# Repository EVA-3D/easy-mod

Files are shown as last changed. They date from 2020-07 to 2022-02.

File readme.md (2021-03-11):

# Rat Rig V-core Pro "Easy Mod"

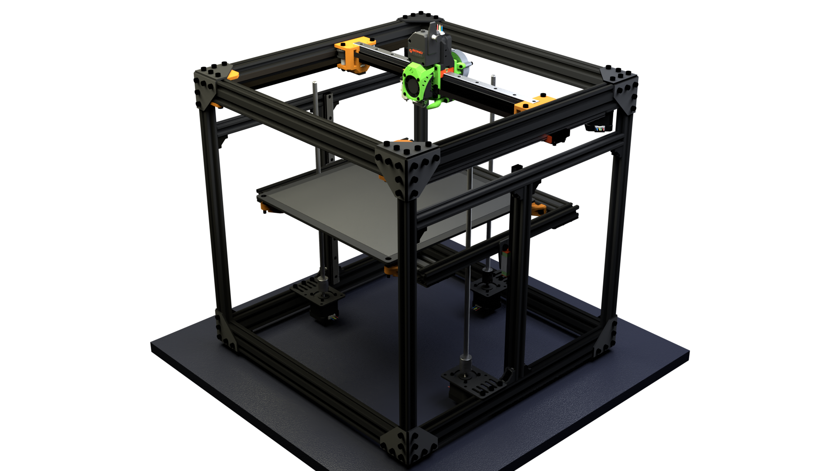
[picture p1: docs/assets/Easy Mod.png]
base


## What this is

Nothing on it's own really - nice selling point I know - but this is a part of a bigger project - the base to use the **[EVA](https://github.com/pkucmus/EVA/) carriage platform** is one example.

The files are in the stl directory, you can download them all as a zip file [here](https://github.com/pkucmus/EVA/archive/master.zip).

## Where to get one

I'm happy to anounce that Rat Rig decided to sell their V-core with Easy Mod out of the box. Check them out to get your V-core Pro with Easy Mod.

## Source

You can find the source in [this Onshape document](https://cad.onshape.com/documents/d1cf51356ca66e6a45738c30/v/f17725bc7d9da347304bc9e4/e/61f36bd0b771bfe27606c238).

## Variants

### 2 Z rails

This is the one I'm currently using, because you need to shorter than the original Z rails (400mm) you need to support them properly so one for each side you'll need:

- 460mm 2020 that goes along the Y axis, under the Y rails
- around 347mm 2020 for the Z axis support of the Z rail, this does not have to be exact and depends on how much space your motors leave you

### 3 Z rails

You just need the extra Z motor assembly (motor, plate, screw and coupler). There is no third 2020 Z extursion on the back required. MGN Z rails constrain the bed enough.

## Contact

If you are looking for a direct contact with me the best place to look is [Rat Rig Unoffcial Discord](https://discord.gg/DcCEk8u).

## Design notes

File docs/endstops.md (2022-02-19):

---
title: Endstops
---
# Endstops

Easy Mod does not come with mechanical switch endstops but here are some simple solutions that address the problem.

## Y min/max 

There's a simple part that can act as a mount to the "angled endstops" [AliExpress](https://www.aliexpress.com/item/32837967235.html)

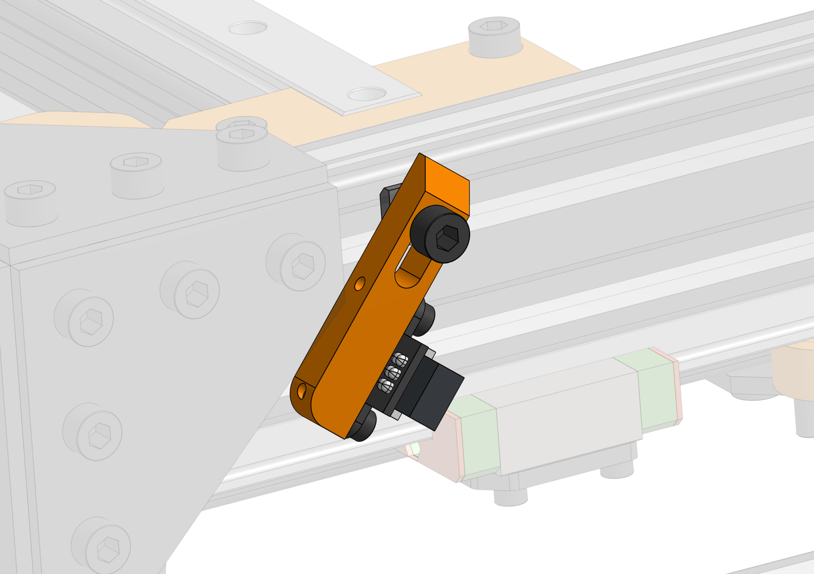
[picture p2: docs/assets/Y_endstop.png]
Y_endstop


## X endstop block

Much like on V-Core 3 you can use a simple stop block for an EVA endstop to bump against.

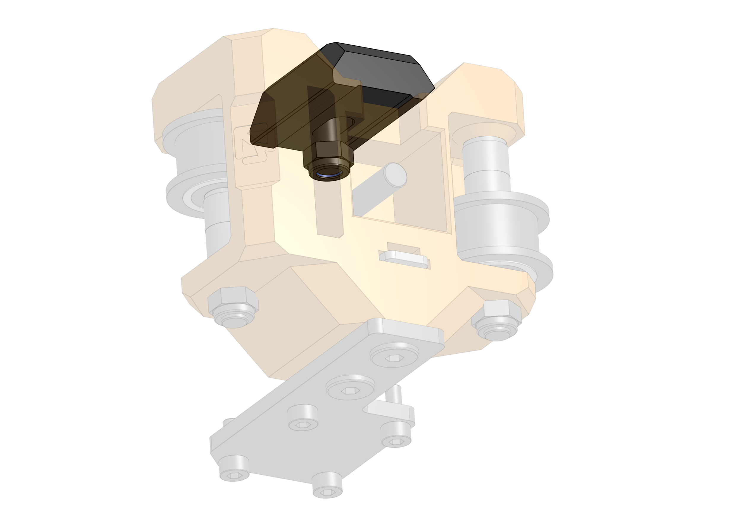
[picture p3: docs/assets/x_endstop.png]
XS_endstop


## Combined BOM

{{ get_bom("endstops") | md_table }}

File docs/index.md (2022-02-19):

---
title: Easy Mod
---
# Easy Mod

"Easy Mod" is a modification for the Rat Rig V-core Pro printer developed by [Paweł Kucmus](https://github.com/pkucmus){target=_blank} and the Rat Rig community. Enables V-core Pro to use the [EVA platform](https://main.eva-3d.page){target=_blank}.

Up to Easy Mod 1.2.1 there is no additional hardware required to use Easy Mod on V-core Pro but 1.2.1 is only compatible with [EVA](https://main.eva-3d.page/){target="_blank"} to to it's 2.3.0 version. Scroll down for more information about the specific versions and what's planned for the future.

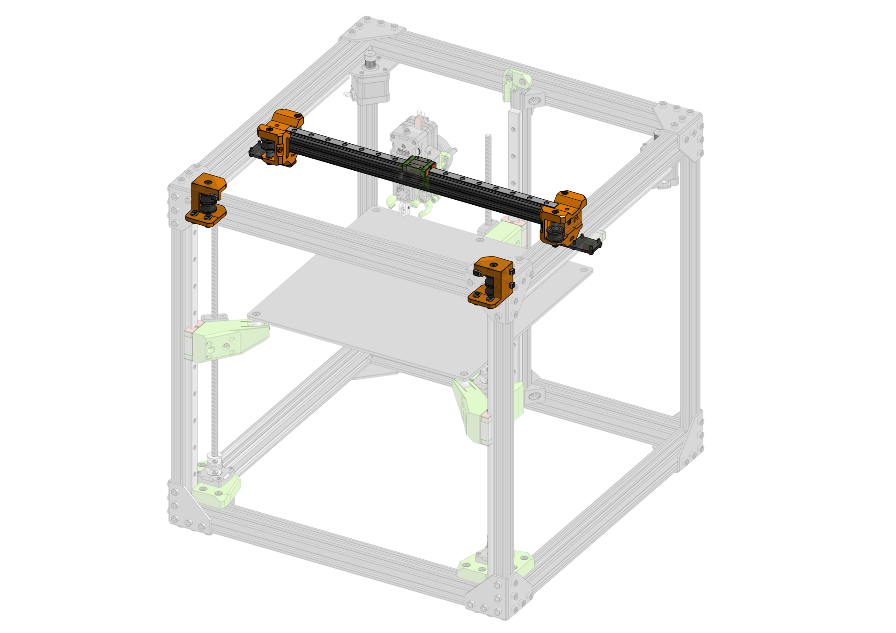
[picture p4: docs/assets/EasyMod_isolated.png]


### Printing

You can print the parts with 0.2mm or even 0.3mm layer height. Use 4 perimeters to make them strong (~1.8mm wall width), infill is not that important - 20% will be fine. **No supports needed**.

### Roadmap

## Attributions

Big thanks to:

- **[Simon Davie](http://www.nexxdesign.co.uk/)** for double checking the measurements and belt paths 
- **top_gun_de** for fixing the belt path in 2.0.1.

## Issues

In case of issues or ideas please file an issue here: https://github.com/EVA-3D/easy-mod/issues

## Contact

If you need a more direct contact I'm on the [Rat Rig Unofficial Discord Server](https://discord.gg/DcCEk8u).

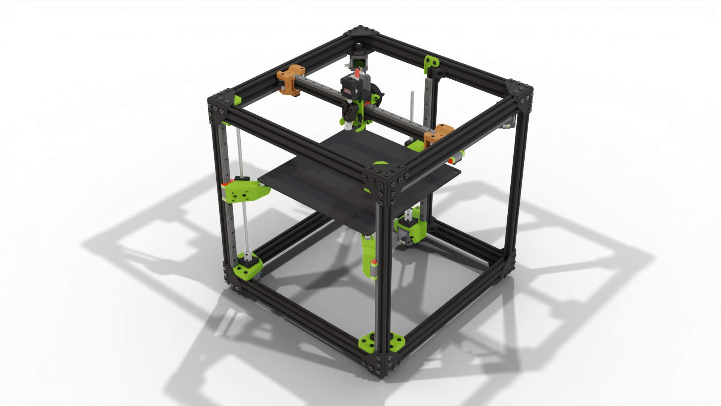
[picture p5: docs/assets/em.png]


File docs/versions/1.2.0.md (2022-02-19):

---
title: 1.2.0
---
# 1.2.0

> Compatibility: EVA < 2.4.0

!!! warning

    To get the files from this version visit the [1.2.0](https://github.com/EVA-3D/easy-mod/tree/release/1.2.0/docs/stls) tag on GitHub.

Added compatibility with the new EVA 2 belt mounting system. 

## Upgrade from 1.1.0

To upgrade one needs to reprint the `xy_joiner` parts. No hardware requirements change in this release.

## BOM

{{ get_bom("1.2.0") | md_table }}

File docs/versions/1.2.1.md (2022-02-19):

---
title: 1.2.1
uid: 1.2.1
---
# 1.2.1 

> Compatibility: EVA < 2.4.0

!!! warning

    To get the files from this version visit the [1.2.1](https://github.com/EVA-3D/easy-mod/tree/1.2.1/docs/stls) tag on GitHub.

This version gives back the Y space that Easy Mod originally stole. To regain that Y one needs to do one of two things:

1. use the included `bed_corner` parts that move the bed -10mm in Y
2. move the whole gantry -10mm in Y (this will be difficult on 3 axis V-core)

I used those `bed_corner` parts for a very long time on my V-core - nothing melted (PETG).

## Upgrade from 1.2.0

The `xy_joiner` parts did not change. The `corner` and `bed` parts are new. 

## BOM

{{ get_bom("1.2.1") | md_table }}

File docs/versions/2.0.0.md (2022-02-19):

---
title: 2.0.0 - 2.0.1
---
# 2.0.0 - 2.0.1

> Compatibility: EVA >= 2.4.0

!!! info "2.0.1 changes"

    The only change (an important one) in 2.0.1 was fixing the belt paths that were not perfect in 2.0.0.

An MGN12 rail is ~60% of the weight of an MGN15 rail. [EVA](https://main.eva-3d.page/){target="_blank"} is dropping support for MGN15 in version 2.4.0 for that and other reasons like easier maintenance. 

To avoid leaving V-Core Pro users locked out from future [EVA](https://main.eva-3d.page/){target="_blank"} updates this *final* version of Easy Mod has been prepared.

## Two variants

To make the transition to MGN12 easier and hopefuly cheaper, two variants of the `xy_joiner` parts are provided. Both variants now has an M5 screw that threads into the ends of the extrusions for an easier and more robust installation.

### Variant A

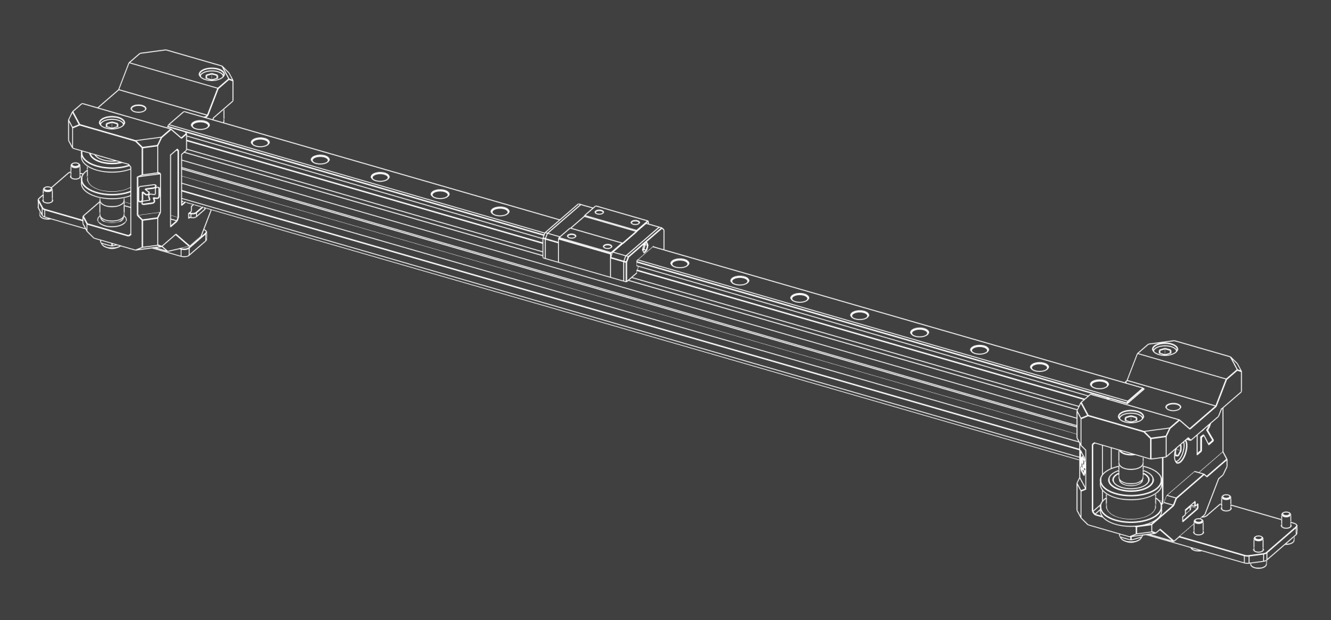
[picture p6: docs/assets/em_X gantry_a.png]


This one is made in the hope that a 400mm rail will be more easily available than a 420mm one, it does however require a new 2020 extrusion. 

| Hardware | Length | Comment |
| --- | --- | --- |
| 2020 extrusion | 420mm | Need to buy |
| MGN12 rail | 400mm | Available at Rat Rig |

#### BOM

{{ get_bom("2.0.0A") | md_table }}

### Variant B

This variant reuses the same 394mm 2020 extrusion but requires a 420mm rail that might be harder to source.

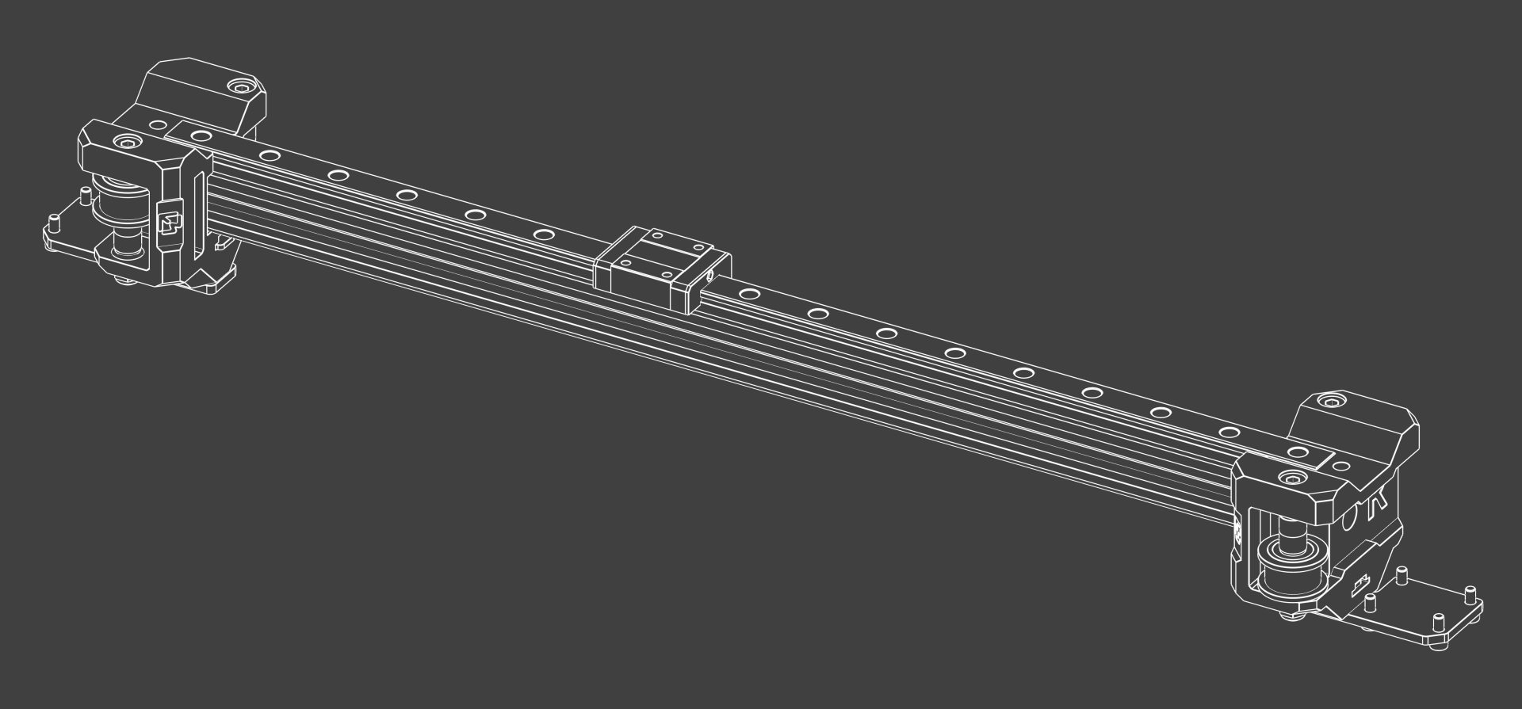
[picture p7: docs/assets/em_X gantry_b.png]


| Hardware | Length | Comment |
| --- | --- | --- |
| 2020 extrusion | 394mm | Same as V-Core Pro |
| MGN12 rail | 420mm | Need to buy |

#### BOM

{{ get_bom("2.0.0B") | md_table }}

## XY Corner Idlers

These have not changed from the previous version, and are still compatible.

## Features

Optional `M5x20mm` screws were added to where the 2020 extrusion ends meet the `xy_joiners`

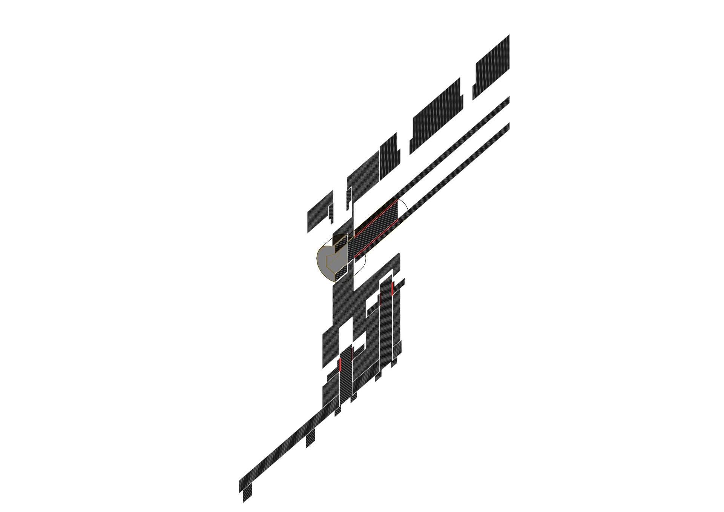
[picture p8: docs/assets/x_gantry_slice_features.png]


The whole design is based of the V-Core 3 design (V-Core 3 ideas started with Easy Mod so it has come full circle now :smile:). With that we have the single M5 bolt on the top of the part, much like on V-Core 3 but due do the differences between the two printers and the B variant, 100% compatibility was not achieved.

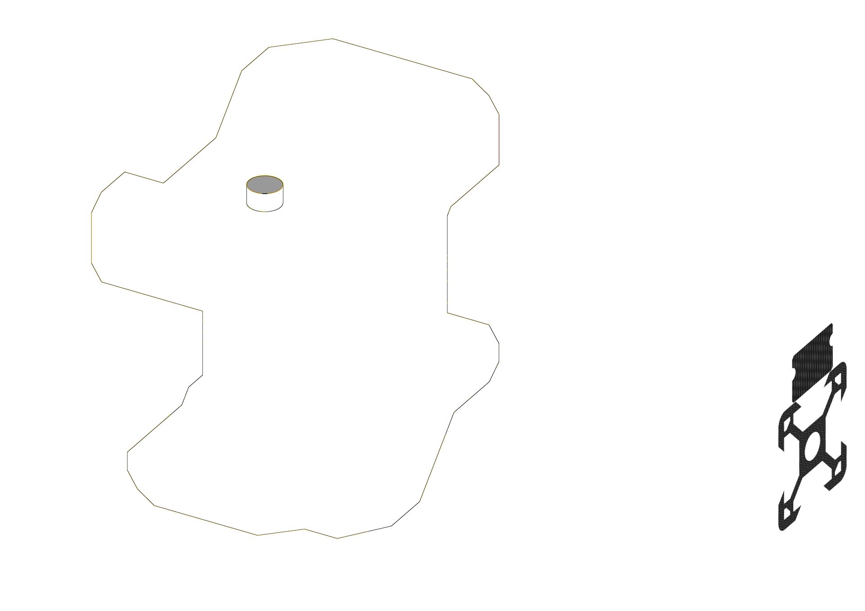
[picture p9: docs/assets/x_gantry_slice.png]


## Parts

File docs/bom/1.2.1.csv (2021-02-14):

Item No. | Quantity | Name | Material
1 | 1 | xy_joiner_left | PETG
2 | 1 | xy_joiner_right | PETG
3 | 1 | corner_left | PETG
4 | 1 | corner_right | PETG
5 | 4 | bed_corner | PETG
6 | 2 | xy_joiner_plate | - None -
7 | 1 | 2020 394 mm | - None -
8 | 4 | v slot slide nut M5 | - None -
9 | 4 | openbuilds_idler_wheel | - None -
10 | 8 | 625 2RS | - None -
11 | 4 | nylon_spacer | - None -
12 | 4 | DIN 912 M5 45 mm | - None -
13 | 8 | DIN 912 M3 8 mm | - None -
14 | 12 | Spacer 1 millimeter | - None -
15 | 8 | Spacer 6 millimeter | - None -
16 | 1 | MGN15 rail 420mm | - None -
17 | 1 | MGN15C carriage body | - None -
18 | 4 | M5 Hex nut Nyloc | - None -

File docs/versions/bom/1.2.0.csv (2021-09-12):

Item No. | Quantity | Name | Material
1 | 1 | xy_joiner_left | - None -
2 | 1 | xy_joiner_right | - None -
3 | 2 | xy_joiner_plate | - None -
4 | 1 | 2020 394 mm | - None -
5 | 4 | v slot slide nut M5 | - None -
6 | 4 | openbuilds_idler_wheel | - None -
7 | 8 | 625 2RS | - None -
8 | 4 | nylon_spacer | - None -
9 | 4 | DIN 912 M5 45 mm | - None -
10 | 8 | DIN 912 M3 8 mm | - None -
11 | 12 | Spacer 1 millimeter | - None -
12 | 8 | Spacer 6 millimeter | - None -
13 | 1 | MGN15 rail 420mm | - None -
14 | 1 | MGN15C carriage body | - None -
15 | 4 | M5 Hex nut Nyloc | - None -

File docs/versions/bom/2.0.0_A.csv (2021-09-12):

Item | Quantity | Name | Material
1 | 1 | 2020 420 mm | - None -
2 | 4 | DIN 912 M5 45 mm | Hardened Alloy Steel
3 | 4 | openbuilds_idler_wheel | - None -
4 | 8 | 625 2RS | - None -
5 | 4 | nylon_spacer | - None -
6 | 4 | v slot slide nut M5 | - None -
7 | 2 | xy_joiner_plate | Aluminum
8 | 1 | xy_joiner_left_a | PETG
9 | 8 | DIN 912 M3 8 mm | Hardened Alloy Steel
10 | 12 | Spacer 1 millimeter | - None -
11 | 8 | Spacer 6 millimeter | - None -
12 | 6 | M5 Hex nut Nyloc | Hardened Alloy Steel
13 | 2 | ISO 898-1 M5 20 mm | - None -
14 | 2 | ISO 898-1 M5 12 mm | - None -
15 | 2 | DIN 912 M5 20 mm | Hardened Alloy Steel
16 | 1 | DIN 912 M5 12 mm | Hardened Alloy Steel
17 | 1 | x_endstop_block | PETG
18 | 1 | MGN12 rail 400mm | - None -
19 | 1 | MGN12C carriage body | - None -
20 | 1 | xy_joiner_right_a | PETG

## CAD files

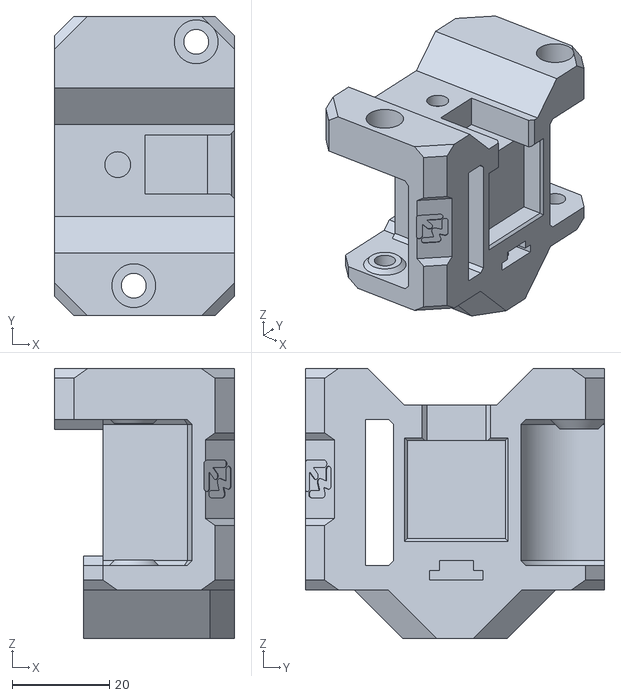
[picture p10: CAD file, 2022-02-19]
docs/versions/2.0.0/stls/xy_joiner_left_b.stl
37.0 x 61.6 x 55.5

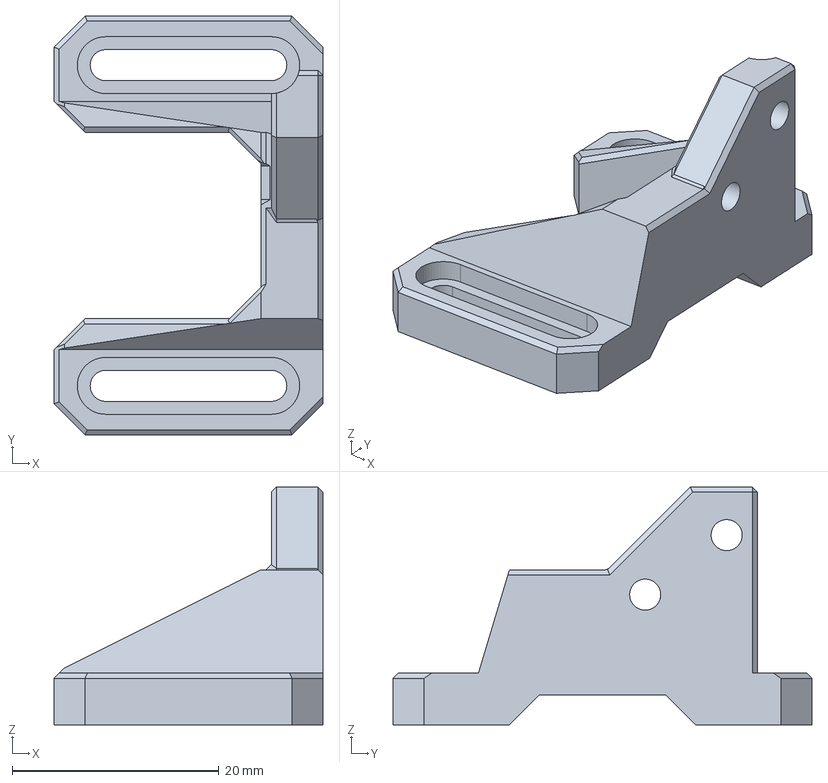
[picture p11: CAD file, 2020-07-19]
step/X endstop block - Endstop block.step
26.0 x 40.5 x 23.0 mm

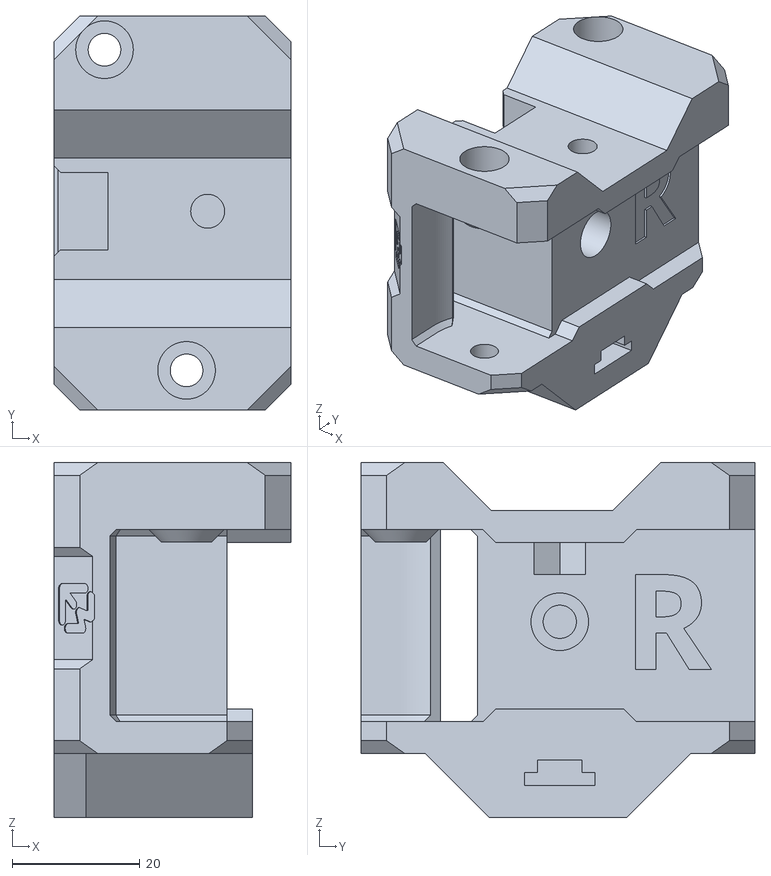
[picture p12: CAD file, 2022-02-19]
docs/versions/2.0.0/stls/xy_joiner_right_a.stl
37.0 x 61.6 x 55.5

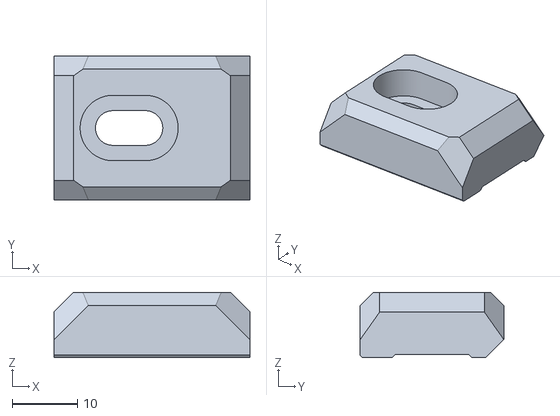
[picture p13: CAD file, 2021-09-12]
docs/versions/2.0.0/stls/x_endstop_block.stl
30.0 x 22.0 x 10.0

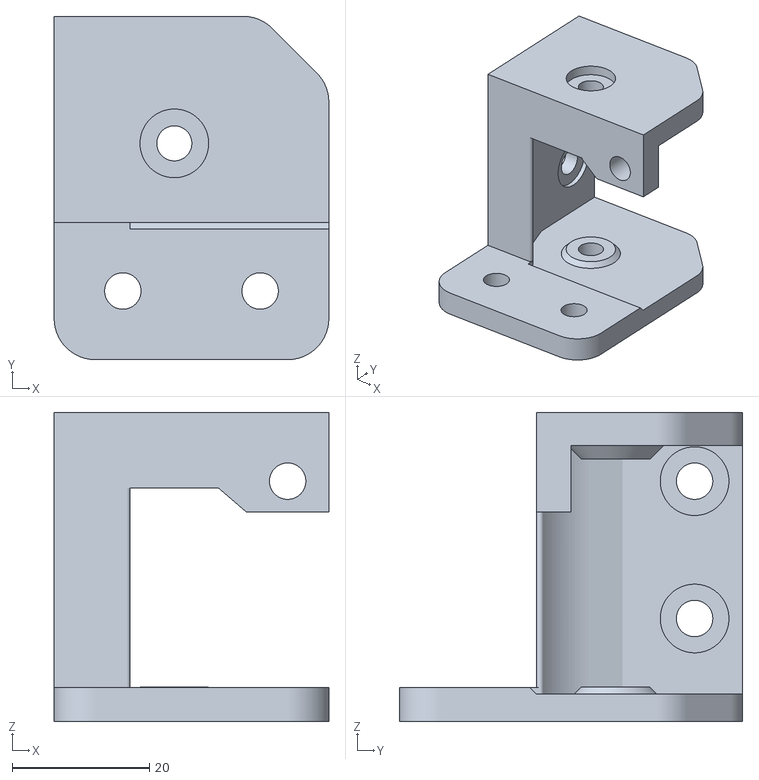
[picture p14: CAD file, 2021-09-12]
docs/versions/2.0.0/stls/corner_right.stl
40.0 x 50.0 x 45.0

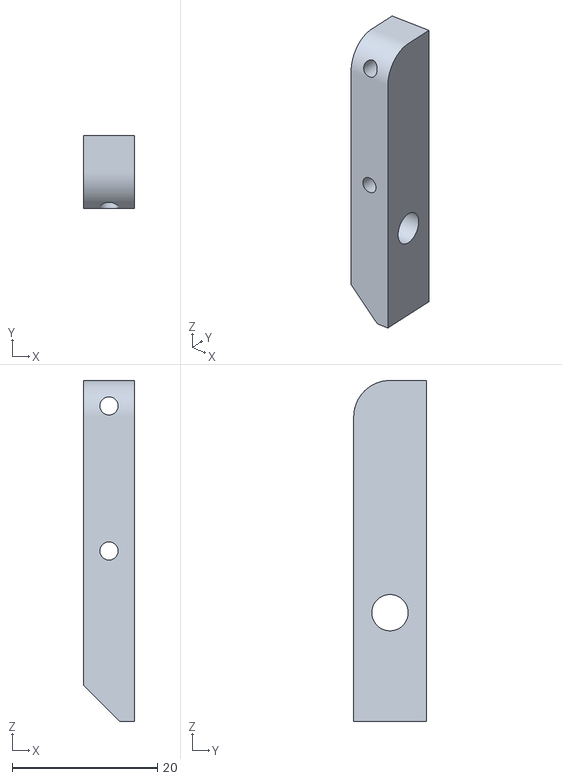
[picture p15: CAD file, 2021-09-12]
docs/versions/2.0.0/stls/y_endstop.stl
7.00 x 10.0 x 47.0

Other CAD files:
docs/versions/2.0.0/stls/xy_joiner_right_b.stl
docs/versions/2.0.0/stls/xy_joiner_left_a.stl
docs/versions/2.0.0/stls/corner_left.stl

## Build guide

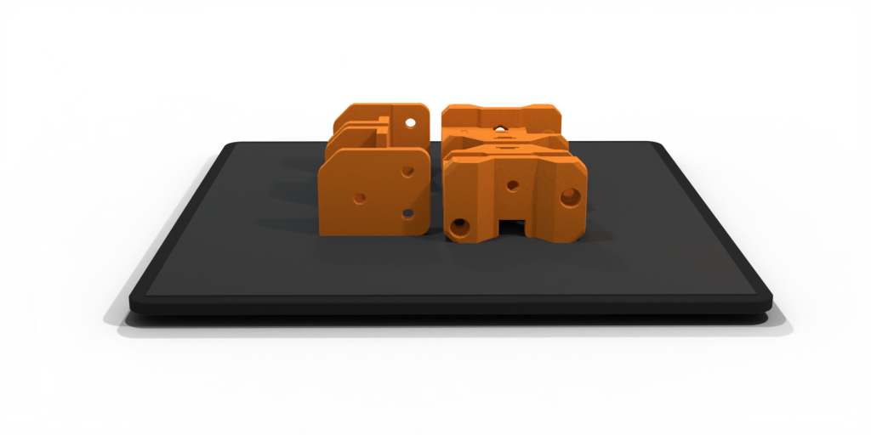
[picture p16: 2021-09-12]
docs/assets/print_orientation/0014.png

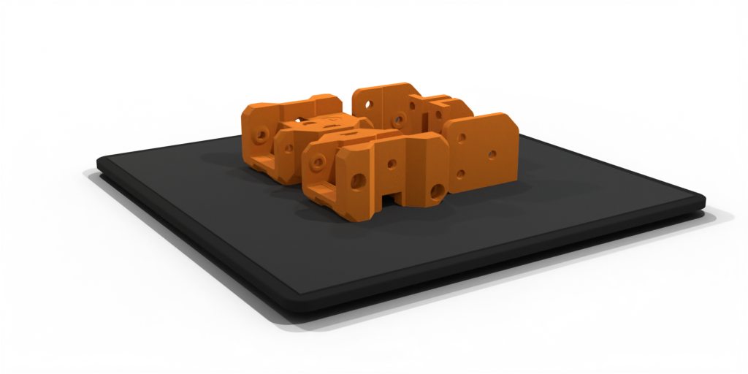
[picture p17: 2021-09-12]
docs/assets/print_orientation/0035.png

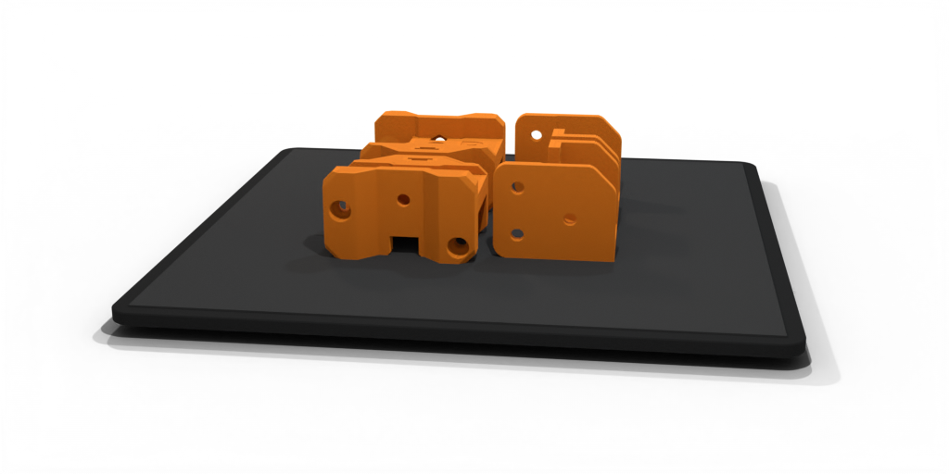
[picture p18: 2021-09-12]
docs/assets/print_orientation/0031.png

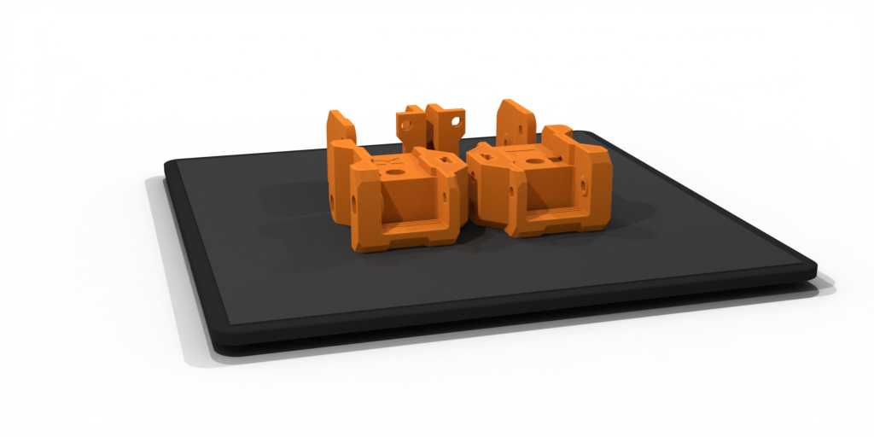
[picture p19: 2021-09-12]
docs/assets/print_orientation/0007.png

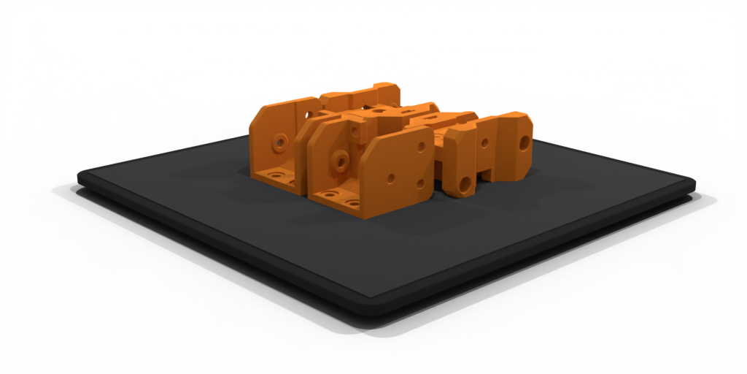
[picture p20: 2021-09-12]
docs/assets/print_orientation/0018.png

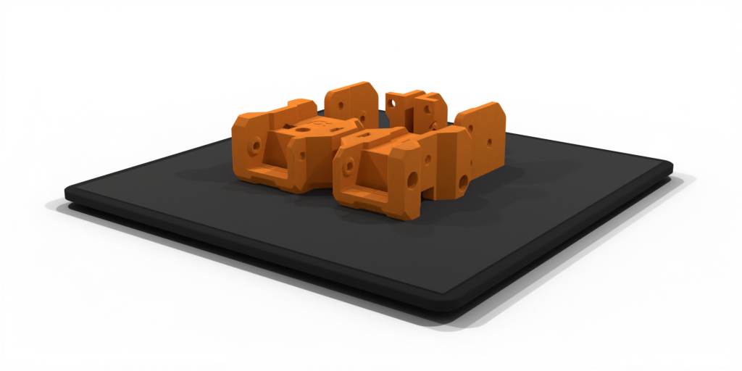
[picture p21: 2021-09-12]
docs/assets/print_orientation/0002.png

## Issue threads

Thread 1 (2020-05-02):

XY motors need to run in reverse

Blue-Dust, 2020-05-02:
When upgrading the V-Core 2.0 to the Easy Mod with Pro upgrade kit, I needed to make both the stepper motors run in reverse to get it to work properly.  You may also have to swap the cables between the X/Y motors, as I may have accidentally swapped them when reconnected the wires.
After reconnecting everything, before making changes, X was working in reverse/mirror and the printer was working as if X Max was actually X Home. Y was homing properly...
I don't consider this to be an issue.  Just something to be aware of if someone runs into the same problem.

pkucmus, 2020-06-04:
Thanks! And sorry for the late reply, I'll try to find time to document that.

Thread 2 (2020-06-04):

Easy-mod on current Linear Rail version of RatRig printer

flajzi, 2020-06-04:
Is actual Easy-Mod valid on current model of Rat Rig V-core Pro printer?
I built latest Rat Rig V-Core Pro and I would like adapt EVA platform, but XY joiners from Easy-Mod are fitted to rail under frame (current V-Core Pro has rails (+XY motors) on frame) nad also you need shorter Z rail.
Do you plan to adjust Easy-mod to current mount of X rail to Y rail (mount on top of XY joiner)?

pkucmus, 2020-06-04:
It is designed for the pro but to mount it you need 2x Y 2020 mounted below the rails and shorter 2020 for Z rails, picture of my V-core Pro for reference.

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

flajzi, 2020-06-04:
Thank you for your quick answer. Is there any advantage (somehow which I can't see) in compare with original mounting where Y rail is on top of 2040 frame?
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

Turricann, 2020-07-16:
I would have to agree on using a top mounted adapter for this mod to mount the linear rails on top there are also other benefits like the rails will run smoother mounted on the top on top, making an enclosure is simpler and would make this a true easy mod.
I know i would start using it if it was designed that way.

my current build state.

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

pkucmus, 2020-07-16:
The main issue with a top mount is that there is no way to reuse the XY plates. You can't (with ease) just flip it around as the plate to joiner M5 screws would interfere with the MGN rail. One would need to use plastic where the plates now are - which is fine but would probably a different mod/project. I there's too much going around EVA right now for me to tackle this.

pkucmus, 2020-07-16:
Also radial and reverse radial load ratings are the same for an MGN rail - gothic arch contact design.
Those can differ on rails for special/other applications but MGN standard has gothic arch.

Turricann, 2020-07-16:
I wouldn't mind fabricating a replacement bracket out of metal after the plastic concept has been proved. I agree on the concept of the rails i just find they run smoother while loaded however I haven't really ran them upside down for a long period.

pkucmus, 2020-07-16:
you could always try flipping the easy mod XY gantry upside down and placing a shorter MGN rail on top - that should work even if only as a proof of concept.

Closed 2025-03-04.

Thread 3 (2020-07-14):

Idlers for MGN12 rails

flajzi, 2020-07-14:
Hi,
could you make alternative version od left/right idlers for MGN12 rails? In EVA project doc you have good point about using MGN12 rails, but Easy-mod is designed for MGN15 rails only.
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

pkucmus, 2020-07-14:
Will do.

Closed 2025-03-04.

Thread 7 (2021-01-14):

OnShape link points to wrong version

tomaski, 2021-01-14:
`readme.md` links to version 1.1.0
should be 1.2.1 https://cad.onshape.com/documents/d1cf51356ca66e6a45738c30/v/f17725bc7d9da347304bc9e4/e/61f36bd0b771bfe27606c238

naorunaoru, 2022-06-02:
I'll bump this one.

Readme points to 1.2.1 but it should be 2.0.1.

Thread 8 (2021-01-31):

Mgn12 C/H versions

EduardoOliveira, 2021-01-31:
Hi,
I just wanted leave the links for a working mgn12 version somewhere people can find them.

This XY joiner version allow for usage of mgn12 on the X axis, all you need if you just want to reduce the axis weight ( https://cad.onshape.com/documents/8559b0e7f5d3b30427c227c5/w/d70f098c5b327e06a1ae23f4/e/12a2436a47701eb37945bb45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 )
If you also have mgn12 C or H in the Y axis you need this adapters, as a replacement for the original RR metal parts ( https://cad.onshape.com/documents/8559b0e7f5d3b30427c227c5/w/d70f098c5b327e06a1ae23f4/e/67166bbf807ca01f4a1ac8b3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 )

This should be related to the old issue #3.

I tried forking the repo and making a pull request but I was unable to work the page generation script, @pkucmus if you teach me how to I can do that if you want.

Once again thank you for the awesome job.

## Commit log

2020-07-19 add step files
    [X endstop block - Endstop block.step, XY Joiner - XY Joiner Left.step, XY Joiner - XY Joiner Right.step]
2020-08-21 Fix belt alignment by making different left and right XY jointers
    [X endstop block - Endstop block.stl, X endstop block - endstop_block.step, X endstop block - endstop_block.stl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]
2020-12-22 remove old and confusing files
    [X endstop block - endstop_block.step, X endstop block - endstop_block.stl, XY Joiner - xy_joiner_left.step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]
2021-01-05 Add bed_corner and xy idler parts, describe 1.2.1
    [1.2.1.csv, BOM_Endstops.csv, bed_corner.stl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]
2021-02-14 Add print setting details
    [1.2.1.csv]
2021-09-12 Deploy 2.0.0
    [1.2.0.csv, 1.2.1.csv, 2.0.0_A.csv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]
2021-09-12 Correct some typos and reference new threaded 2020
2022-02-19 bump docs builder, use db, update the xy joiners
    [BOM_Endstops.csv, xy_joiner_left_a.stl, xy_joiner_left_b.stl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]
2022-05-21 fix broken stl links
    [corner_left.stl, corner_right.stl, x_endstop_block.stl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]
